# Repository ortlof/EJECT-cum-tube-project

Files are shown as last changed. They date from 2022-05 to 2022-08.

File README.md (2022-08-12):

# Project: EJECT
## The Official OSSM automatic realistic emissions project

Peristaltic Lube Pump with 3/8 Silikone Tubing Capable of 4L/min for Countinues Lubing or Creampiesimulation.

Quote from KinkMakers Discord: 

>The TL:DR on a 3/8" tubing modified BD Chance L or Rex L is, well, the pump is the limiting factor, and the reduction right at the end rather than being the entire tubing length >makes for a hell of a shot, provided that's what you're going for. It runs almost the same speed as the pump unloaded as with a toy on the end, which is to say, using a decently >thick mixture of X-lube, about 4L/min. More than enough to satisfy all but the most extreme cases of cream-pies, bordering into straight "Cum inflation" territory.

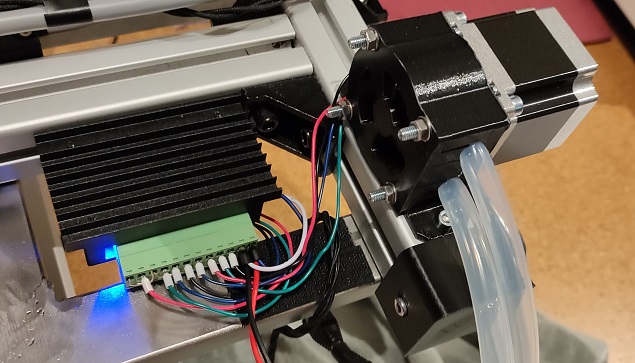
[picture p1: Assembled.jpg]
Final Addon Housing Motor


Max Power Possible with Thick Mixture of X-Lube is 4L/min.

Mainbranch is M5Stamp C3 -> ESP32 Branch is here https://github.com/ortlof/OSSM-Cum-Addon/tree/esp32dev

# Electrical Parts Needed:

| Quantity | Part | Sourcing EU | Price € |
|---|---|---|---|
| 1x | Nema 23 1,26Nm 2.8A 6,35mm Shaft | https://www.amazon.de/gp/product/B06XVC23Z7/ | 23.99 € | 
| 1x | TB6600 4A 9-42V Driver | https://www.amazon.de/gp/product/B095RNPBYN | 10,99 € |
| 1x | I2C Logik Level Converter | https://www.amazon.de/ARCELI-Converter-Bidirektionales-Shifter-Arduino/dp/B07RDHR315 | 0,6 € |
| 1x | LM7805 | https://www.amazon.de/St%C3%BCck-L7805-LM7805-7805-Spannungsregler-default/dp/B08Q8K5342 | 0,7 € |
| 1x | M5Stamp C3 |  https://www.robotshop.com/de/de/m5stamp-c3-mate-mit-stiftleisten.html | 8,26 € | 
| 1x | Soilder Breadboard | https://www.amazon.de/AZDelivery-Lochrasterplatte-Lochrasterplatine-Leiterplatte-Arduino/dp/B078HV79XX/ | 1 € |

# Connection Diagram:

Connect Stepper Pins to Level Shivter to C3 Stamp 

| Stepper PIN | Level Shiverter Hi | Level Shivter LOW | C3 Stamp |
|-|-|-|-|
| - | 5V | - | 5V | 
| - | - | 3,3V | 3,3 V |
| Bride to all Pins | GND | GND | GND |
| PUL + | HV1 | LV1 | 4 |
| DIR + | HV2 | LV2 | 5 |
| ENA + | HV3 | LV3 | 6 | 

LM7805 Check Datasheet for Pinout normaly Top Sight from left to right is: 

| Input | Ground | Output |
|-|-|-|
| 12V Parrallel on Driver | GND Parrallel on Driver on C3 Stamp| 5V to C3 

# Hardware Needed:

Nema 23 Peristaltic Pump comes from this Thingivers: https://www.thingiverse.com/thing:4797064

Parts to Buy 
| Quantity | Part | Sourcing EU | Price € |
|---|---|---|---|
| 9x | 625RS | https://www.amazon.de/Kugellager-Rillenkugellager-gummibeschichtetes-Metalllager-Hobby-Projekte/dp/B07TSP8SBP| 8 € |
| 3x | M5x25 Screw + Nut for Rotor | | | 
| 2x | M2 Screw | ||
| 2x | M2 Heat Set Nut | https://www.amazon.de/ruthex-Gewindeeinsatz-St%C3%BCck-Gewindebuchsen-Kunststoffteile/dp/B088QJG676/
| 4x | M5x45 Screw + Nut || 
| 1x | 9mm ID x OD 12mm Siliconetube food safe Qualtiy | https://www.amazon.de/gp/product/B07T12V62M/ | 10 € |

# 3D Printed Parts:

| Quantity | Part | Info | 3D Print Paramters 
|---|---|---|---|
|1x | Housing_cover | | 6 Wall Layers 28% Infill PLA no Supports |
| 1x | Housing_motor_side or Housing Tubes UP | Depens on you mouting postion see picture | 6 Wall Layers 28% Infill PLA no Supports |
| 1x | Rotor | Depents on you shaft of stepper| 6 Wall Layers 28% Infill PLA With Supports |

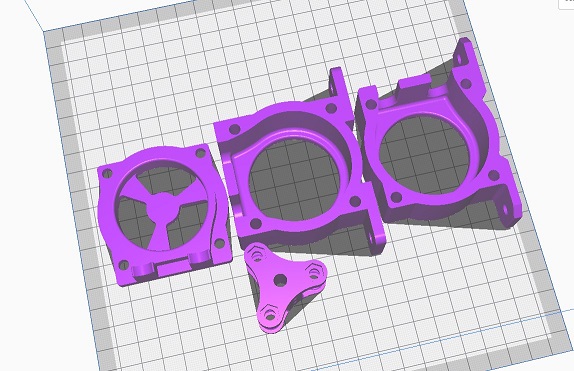
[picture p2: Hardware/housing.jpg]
Housing Motor


# Assembly:

1. Heatset M2 Nut into Rotor Holes on Side 
2. Put Bearing in Rotor with M5x25 Screw and Nut Screw 3 Times 
3. Put Rotor on Stepper and Tighten with M2 Screws. 
4. Put Housing on over rotor to Stepper 
5. Put Tubing in between housing and Bearing 
6. Close Housing with M5 Screw

# Dip Swtiches on tb6600

1 2 3 4 OFF 
5 6 ON

# Software:

Software is right now in State with the OSSM M5 Remote https://github.com/ortlof/OSSM-M5-Remote
Clone the git in folder Cumpump and open Workspace with VS Code and Flash with plaformio.
Right now you need to Hard Code MAC Adresses.

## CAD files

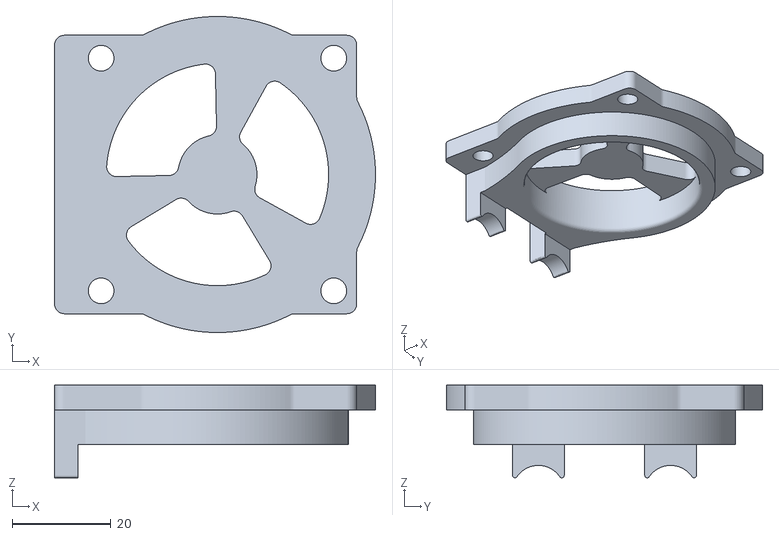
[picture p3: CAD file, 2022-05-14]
Hardware/housing_cover.stl
65.0 x 64.0 x 18.8

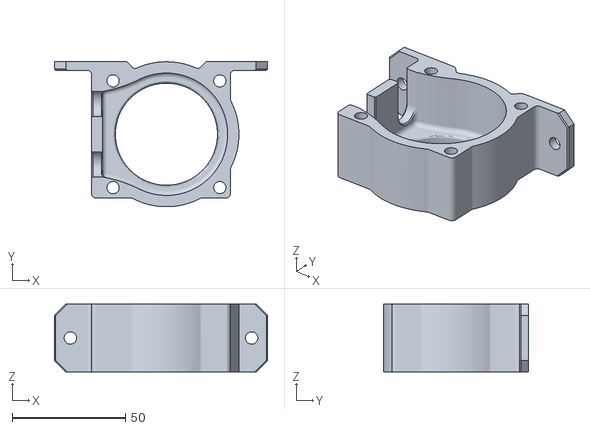
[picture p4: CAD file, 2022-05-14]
Hardware/housing_motor_side.stl
94.0 x 64.2 x 30.0

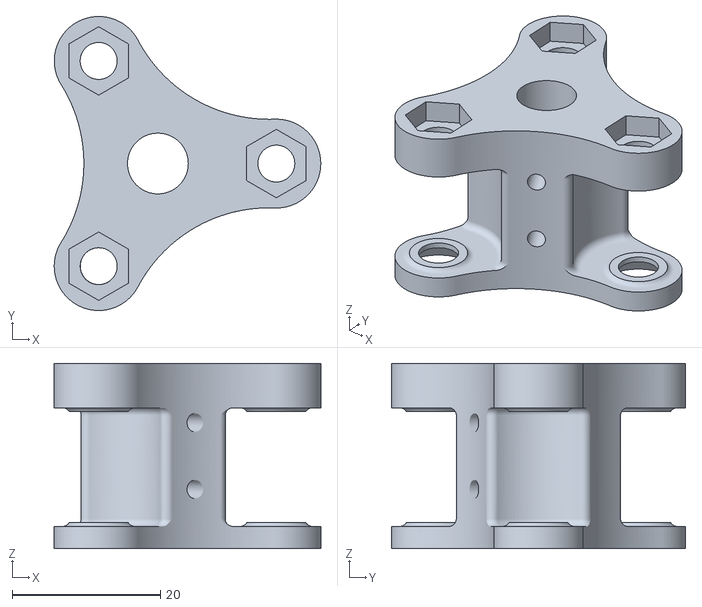
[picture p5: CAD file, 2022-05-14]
Hardware/rotor.stl
36.0 x 39.7 x 25.0

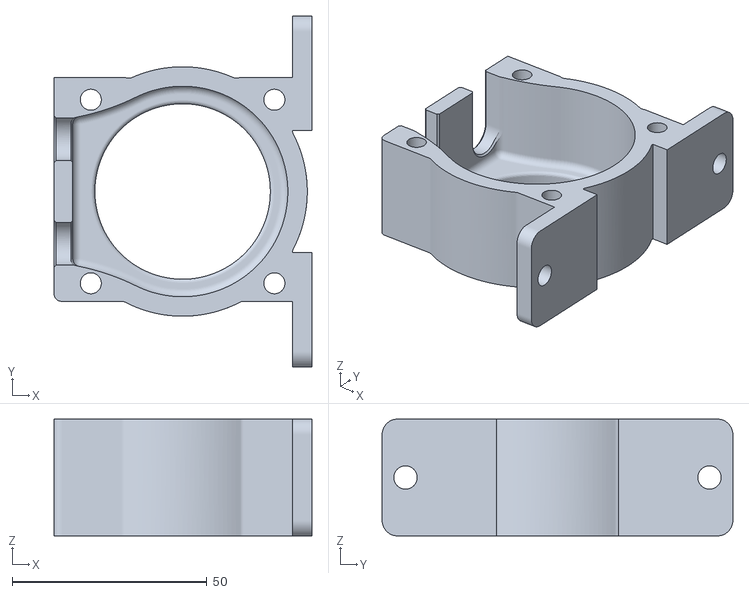
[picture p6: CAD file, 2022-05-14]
Hardware/housing_motor_side_tubes_upside.stl
66.2 x 90.0 x 30.0

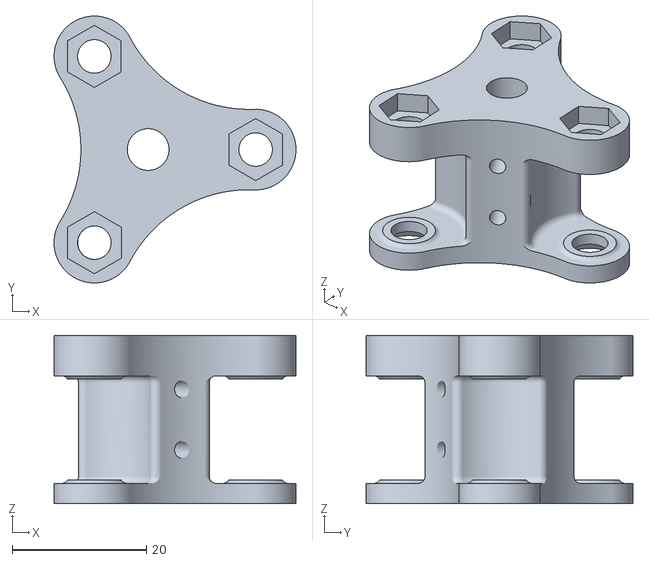
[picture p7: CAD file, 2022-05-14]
Hardware/rotor_6mm_shaft.stl
36.0 x 39.7 x 25.0

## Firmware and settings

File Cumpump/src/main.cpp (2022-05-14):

#include <Arduino.h>          // Basic Needs

// Include the Stepper library:
#include <ESP_FlexyStepper.h>
#include <esp_now.h>
#include <WiFi.h>

// IO pin assignments
const int MOTOR_STEP_PIN = 4;
const int MOTOR_DIRECTION_PIN = 5;
const int MOTOR_ENA_PIN = 6;

uint8_t M5_Remote_Address[] = {0x08, 0x3A, 0xF2, 0x68, 0x1E, 0x74};

// create the stepper motor object
ESP_FlexyStepper stepper;

// Command States

#define CUMSPEED  20
#define CUMTIME   21
#define CUMSIZE   22
#define CUMACCEL  23


unsigned long previousMillis = 0;
long interval = 1000;

///////////////////////////////////////////
////
////  To Debug or not to Debug
////
///////////////////////////////////////////

// Uncomment the following line if you wish to print DEBUG info
#define DEBUG 

#ifdef DEBUG
#define LogDebug(...) Serial.println(__VA_ARGS__)
#define LogDebugFormatted(...) Serial.printf(__VA_ARGS__)
#else
#define LogDebug(...) ((void)0)
#define LogDebugFormatted(...) ((void)0)
#endif

float cum_time = 0.0;
float cum_speed = 1000.0;
float cum_size = 0.0;
float cum_accel = 0.0;

// Variable to store if sending data was successful
String success;

int out_esp_command;
float out_esp_value;

int incoming_esp_command;
float incoming_esp_value;

typedef struct struct_message {
  float esp_speed;
  float esp_depth;
  float esp_stroke;
  float esp_sensation;
  float esp_pattern;
  bool esp_rstate;
  bool esp_connected;
  int esp_command;
  float esp_value;
} struct_message;

bool esp_connect = false;

struct_message outgoingcontrol;
struct_message incomingcontrol;

esp_now_peer_info_t peerInfo;

// Callback when data is sent
void OnDataSent(const uint8_t *mac_addr, esp_now_send_status_t status) {
  Serial.print("\r\nLast Packet Send Status:\t");
  Serial.println(status == ESP_NOW_SEND_SUCCESS ? "Delivery Success" : "Delivery Fail");
  if (status ==0){
    success = "Delivery Success :)";
  }
  else{
    success = "Delivery Fail :(";
  }
}

// Callback when data is received
void OnDataRecv(const uint8_t * mac, const uint8_t *incomingData, int len) {
  memcpy(&incomingcontrol, incomingData, sizeof(incomingcontrol));

  LogDebug(incomingcontrol.esp_command);
  LogDebug(incomingcontrol.esp_value);

  switch(incomingcontrol.esp_command)
  {
    case CUMSPEED:
    {
     cum_speed = incomingcontrol.esp_value;
    }
    break;
    case CUMTIME:
    {
     interval = incomingcontrol.esp_value * 1000;
    }
    break;
    case CUMSIZE:
    {
     cum_size = incomingcontrol.esp_value * 1500;
    }
    break;
    case CUMACCEL:
    {
    cum_accel = incomingcontrol.esp_value * 10000;
    }
    break;
  }
}


void setup()
{  
    Serial.begin(115200);
    WiFi.mode(WIFI_STA);
    LogDebug(WiFi.macAddress());
    
    // Init ESP-NOW
    if (esp_now_init() != ESP_OK) {
    Serial.println("Error initializing ESP-NOW");
    return;
    }
    // Once ESPNow is successfully Init, we will register for Send CB to
    // get the status of Trasnmitted packet
    esp_now_register_send_cb(OnDataSent);

    // Register peer
    memcpy(peerInfo.peer_addr, M5_Remote_Address, 6);
    peerInfo.channel = 0;  
    peerInfo.encrypt = false;
  
      // Add peer        
    if (esp_now_add_peer(&peerInfo) != ESP_OK){
    Serial.println("Failed to add peer");
    return;
    }
    // Register for a callback function that will be called when data is received
    esp_now_register_recv_cb(OnDataRecv);


    // connect and configure the stepper motor to its IO pins
    pinMode(MOTOR_ENA_PIN, OUTPUT);
    digitalWrite(MOTOR_ENA_PIN, LOW);
    stepper.connectToPins(MOTOR_STEP_PIN, MOTOR_DIRECTION_PIN);
}

void loop()
{
  stepper.setSpeedInStepsPerSecond(cum_speed);
  stepper.setAccelerationInStepsPerSecondPerSecond(cum_accel);
  stepper.setDecelerationInStepsPerSecondPerSecond(cum_accel);

  unsigned long currentMillis = millis();
  if (currentMillis - previousMillis >= interval)
  {
    digitalWrite(MOTOR_ENA_PIN, LOW);
    previousMillis = currentMillis;
    stepper.moveRelativeInSteps(cum_size);
  }
  if (stepper.getDistanceToTargetSigned() == 0){
     digitalWrite(MOTOR_ENA_PIN, HIGH);
  }
  
}

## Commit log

2022-05-14 Update to V1
    Update Readme, Cleanup Old folders. Added STLs
    [housing_cover.stl, housing_motor_side.stl, housing_motor_side_tubes_upside.stl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]
2022-06-12 Readme Update ESP32Dev
